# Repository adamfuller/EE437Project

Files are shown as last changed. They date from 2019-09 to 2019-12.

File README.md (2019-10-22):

# EE437Project
Autonomous robot car with a smartphone interface

# TODO
- [x] Code for servo
- [x] Add screw holes to board (Adam - 10/16)
- [x] Incorporate Arduino IC into board (Adam - 10/15)
- [x] Add signal lights (forward, backward, turn)
- [x] Design signal lights board
- [ ] Finalize Controller Board Design
- [ ] Submit board design and parts list
- [ ] Assemble board
- [ ] Test board

# Parts List
## Controller Board
- [ ] 1x ATMega328 IC
- [ ] 1x 16 MHz Crystal
- [ ] 1x 28pin socket
- [ ] 1x 4 pin header - male
- [ ] 1x 3 pin header - male
- [ ] 1x 6 pin header - female 90°
- [ ] 2x 2 slot terminal blocks
- [ ] 2x 2x6 header - male
- [ ] 1x power jack
- [ ] 8x 1n4004 diodes
- [ ] 2x 220uF capacitor
- [ ] 2x 20pF capacitor
- [ ] 2x 1k resistor
- [ ] 1x 2k resistor
- [ ] 1x 5mm LED
- [ ] Wire

## Signal Lights Board
- [ ] 12x 5mm LED
- [ ] 4x 300 resistor
- [ ] 4x 4 pin header - male

# Stand-alone Custom Board
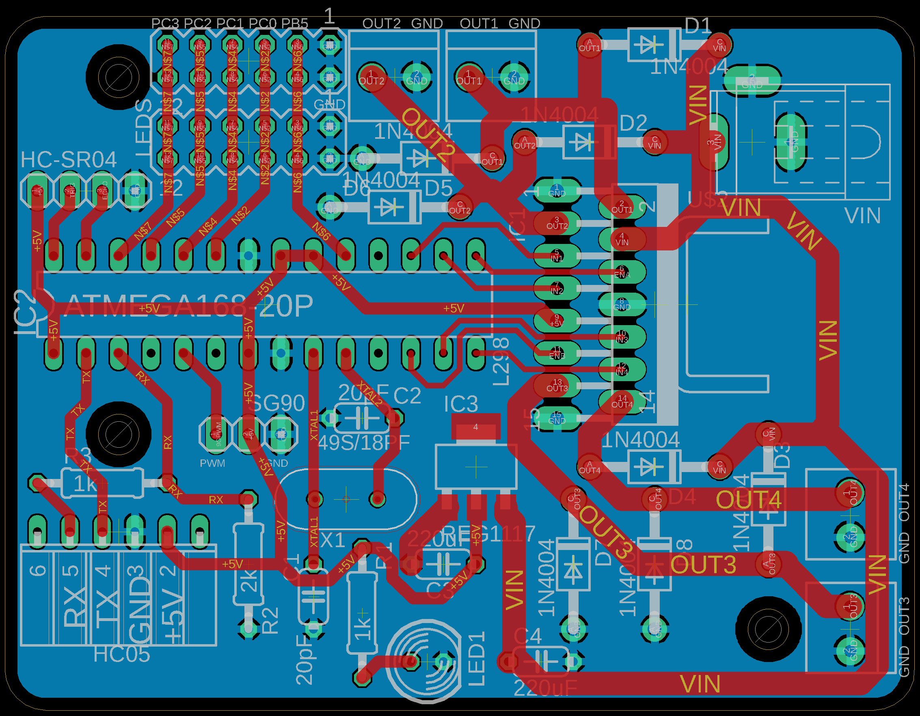
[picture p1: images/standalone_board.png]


# Stand-alone Custom Board Schematic
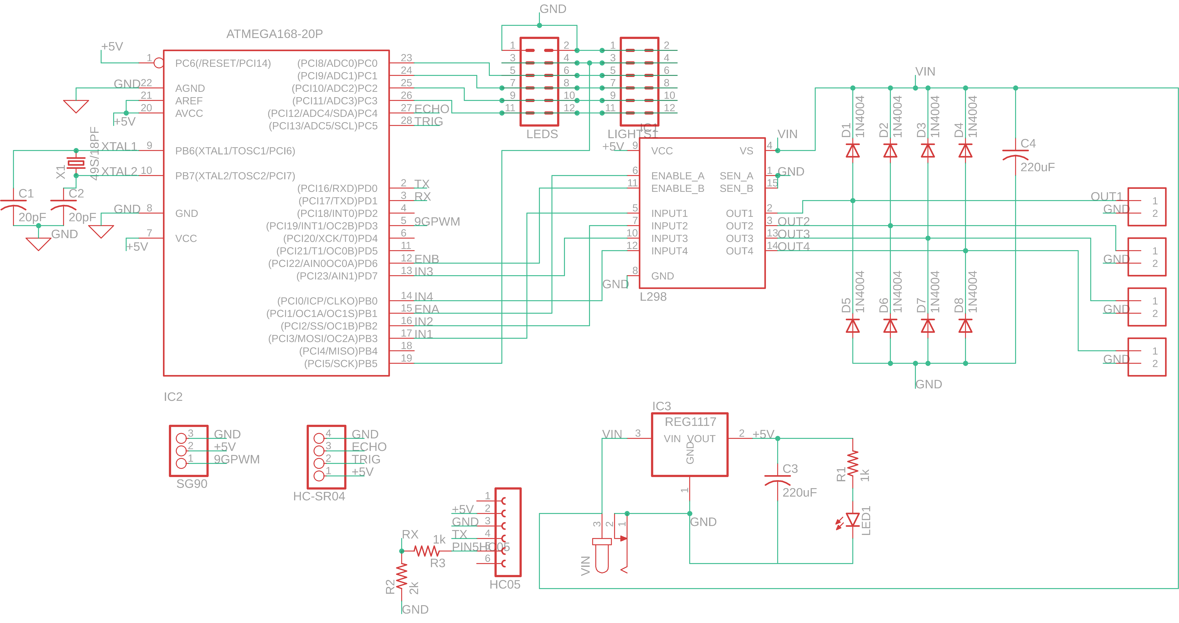
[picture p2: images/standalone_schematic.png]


# Stand-alone Custom Board Manufacturing Preview

## Top
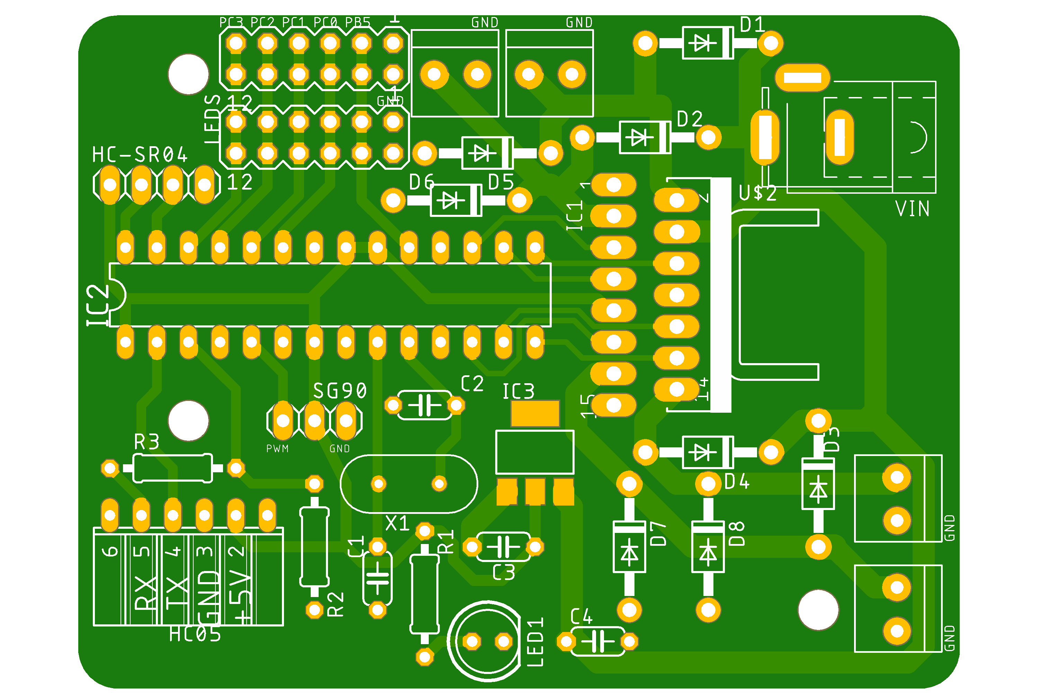
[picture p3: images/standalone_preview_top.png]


## Bottom
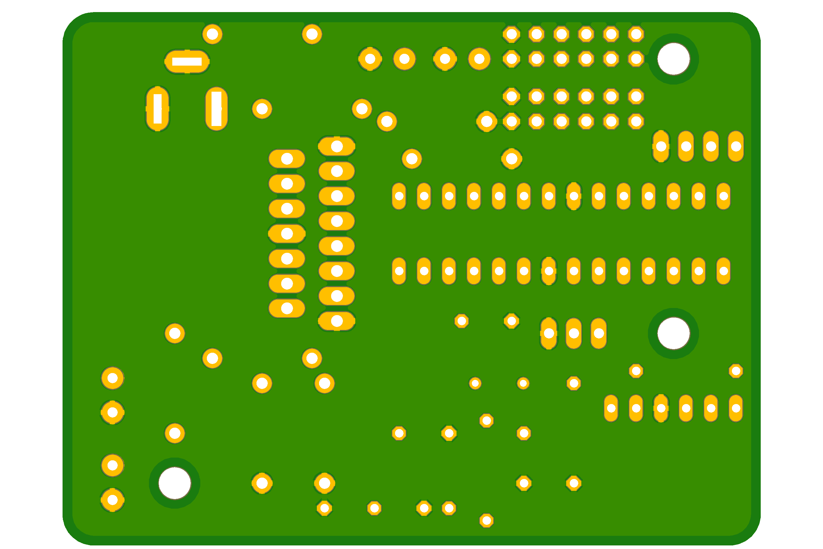
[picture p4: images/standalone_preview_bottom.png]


# Custom Shield Board
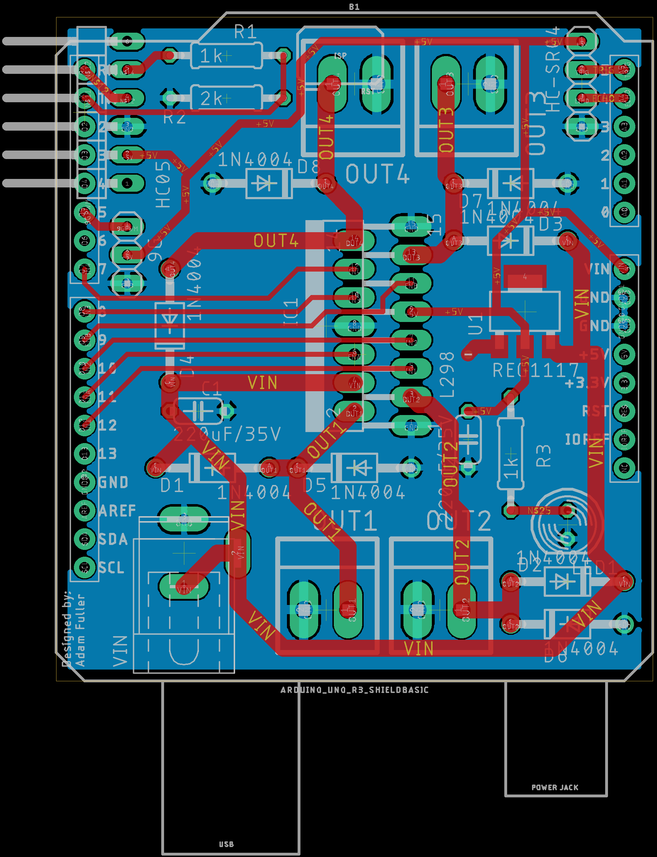
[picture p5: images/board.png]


# Custom Shield Schematic
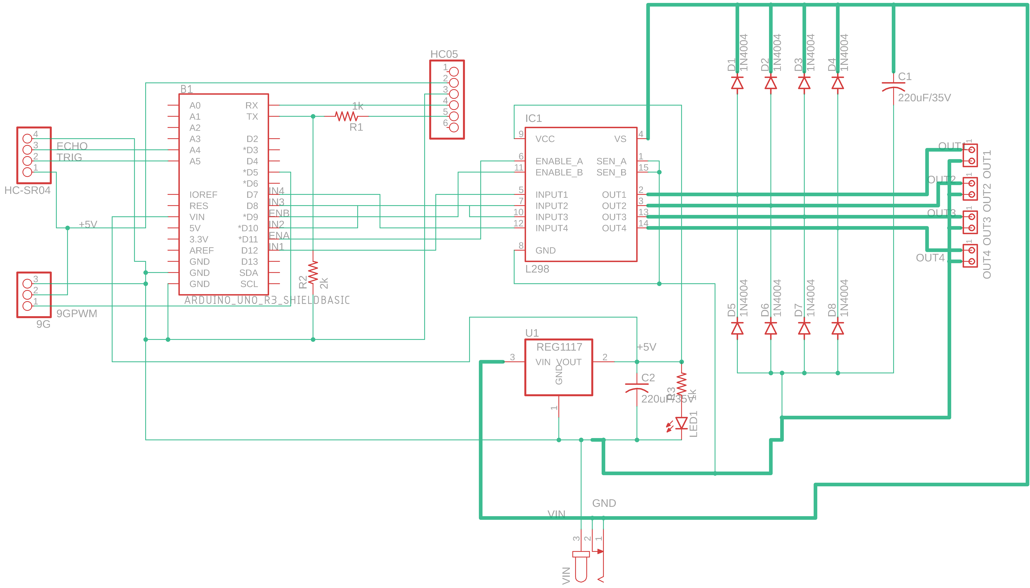
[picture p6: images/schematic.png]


# Custom Shield Manufacturing Preview

## Top
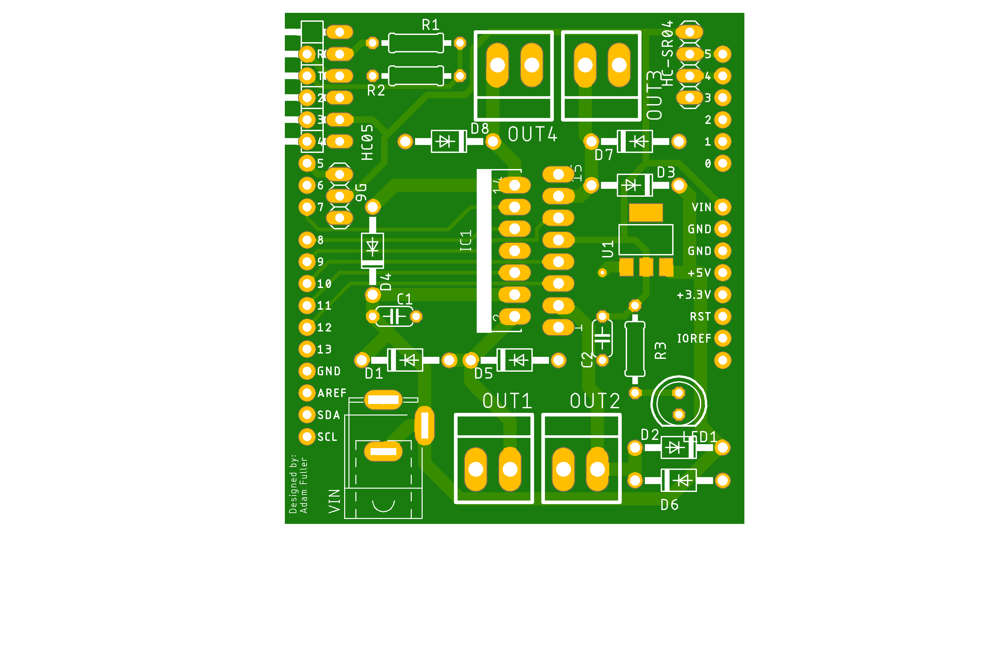
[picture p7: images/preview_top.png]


## Bottom
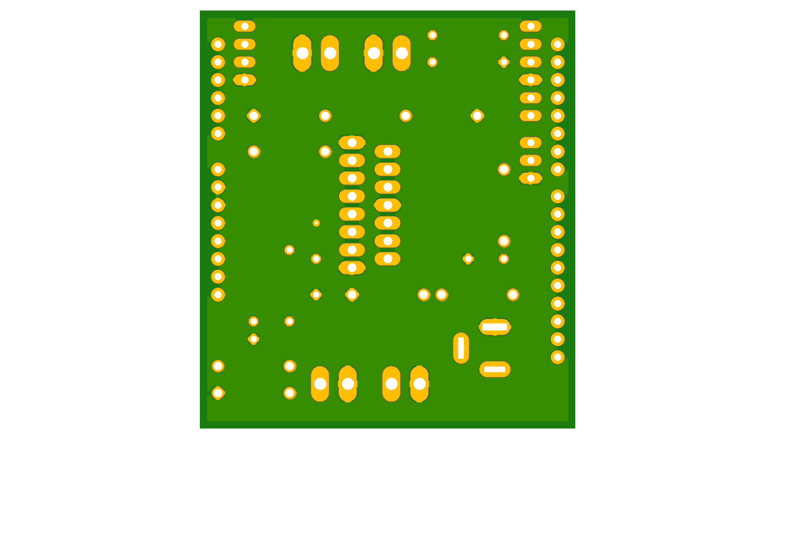
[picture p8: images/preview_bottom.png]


# Reduced Custom Board
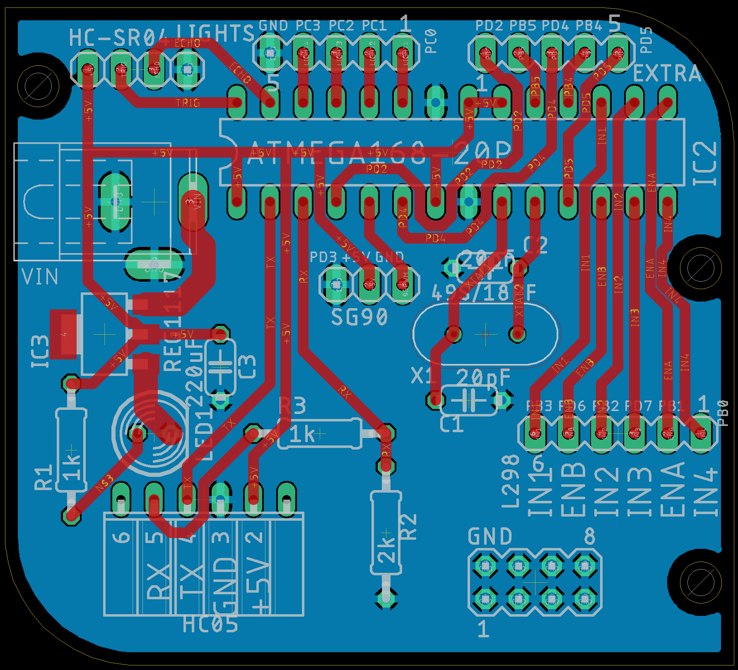
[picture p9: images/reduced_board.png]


# Reduced Custom Board Schematic
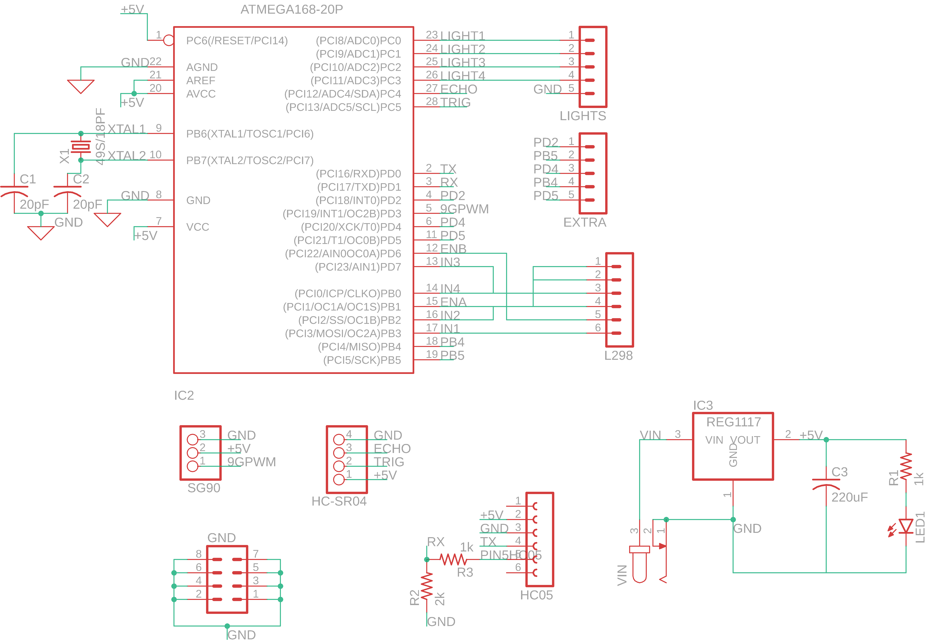
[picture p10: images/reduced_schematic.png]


# Reduced Custom Board Manufacturing Preview

## Top
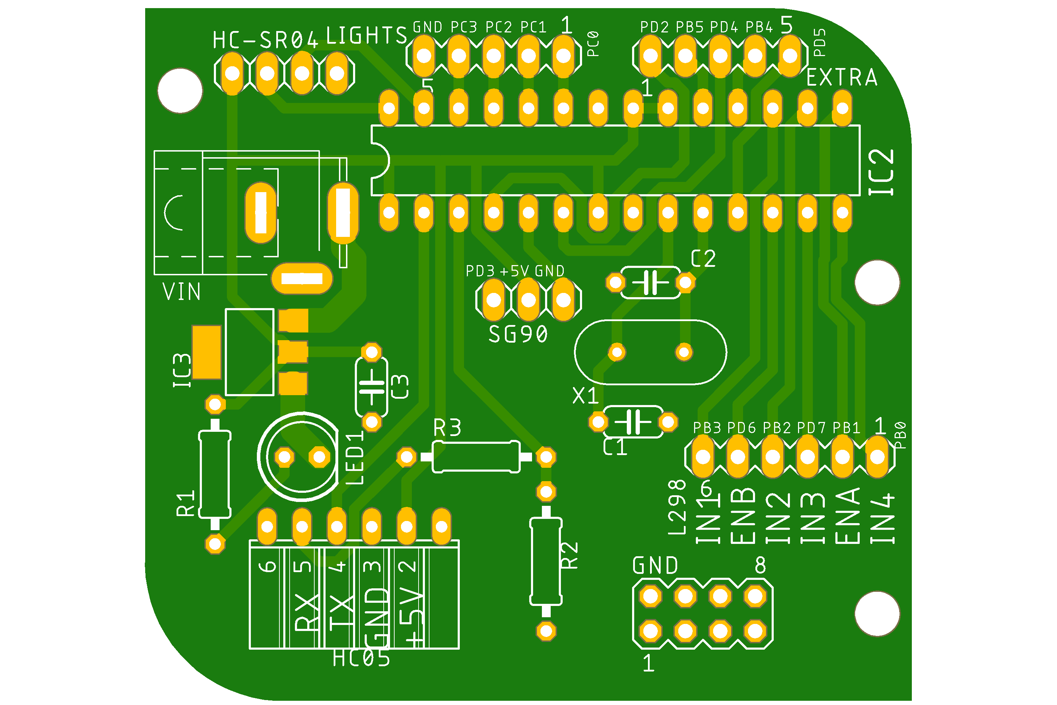
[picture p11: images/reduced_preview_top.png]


## Bottom
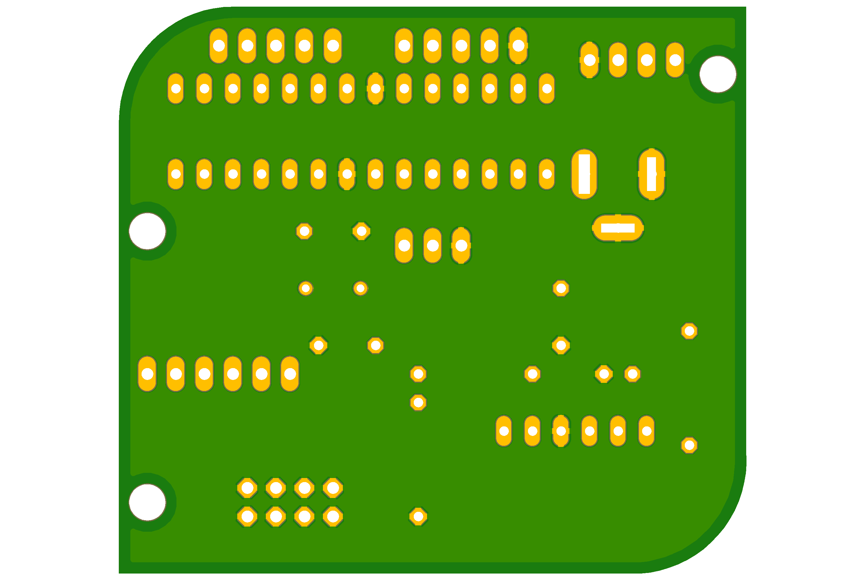
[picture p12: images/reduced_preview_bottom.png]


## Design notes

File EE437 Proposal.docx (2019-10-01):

EE437 Team 5

Adam Fuller

Isaiah Chamoun

Gavin Matthews

Description:

The project chosen by the members of Team 5 is titled “Autonomous robot car with a smartphone interface.” The goal of our project is to develop an application to control a 4-wheeled car as well as the Arduino code to interface with this. The phone and the car should communicate using Bluetooth. The minimum functionality of the car is to be capable of driving forward, backwards, turning right and left, as well as stopping. The car should communicate with an ultrasonic distance sensor to prevent itself from being driven into obstacles. A custom PCB will be designed to house the connections to the Bluetooth module, ultrasonic sensor, and the controls for the motor driver.

Parts List:

2x 8 Pin Header

1x 10 Pin Header

1x 6 Pin Header

2x 1 kΩ Resistor

1x 2 kΩ Resistor

8x 1N4004 Diodes

2x 2 Pin Terminal Block

1x 5mm Green LED

2x 220 µF 35V Capacitor

1x L298 IC

1x REG1117 Voltage Regulator

1x HC-SR04 Ultra sonic sensor

1x HC-05 Bluetooth module

4x DC Motors

1x SG90 Servo Motor

2x 18650 Batteries

1x Custom PCB

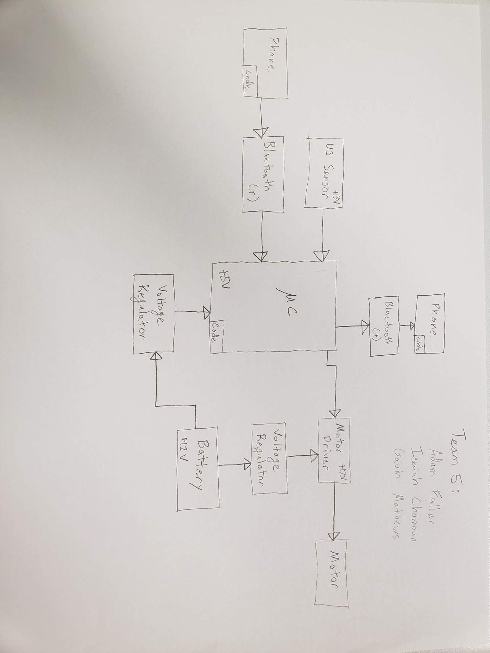
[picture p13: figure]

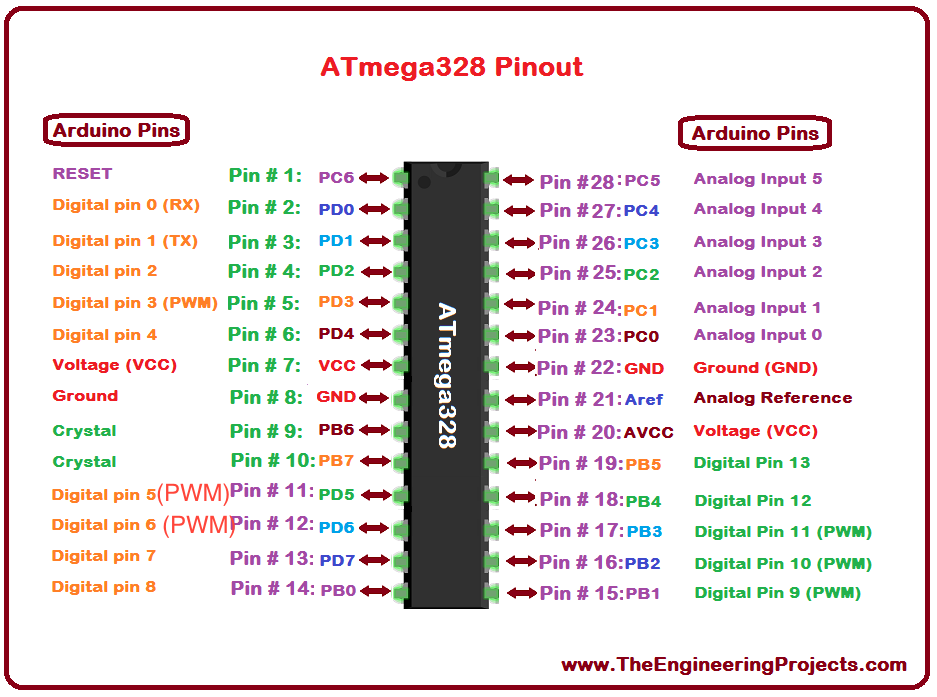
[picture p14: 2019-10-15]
images/ATmega328-Pinout.png

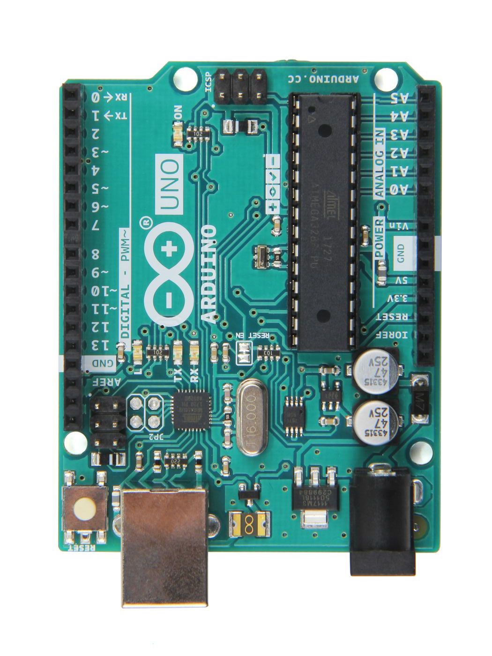
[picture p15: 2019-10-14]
images/arduinoUno.jpg

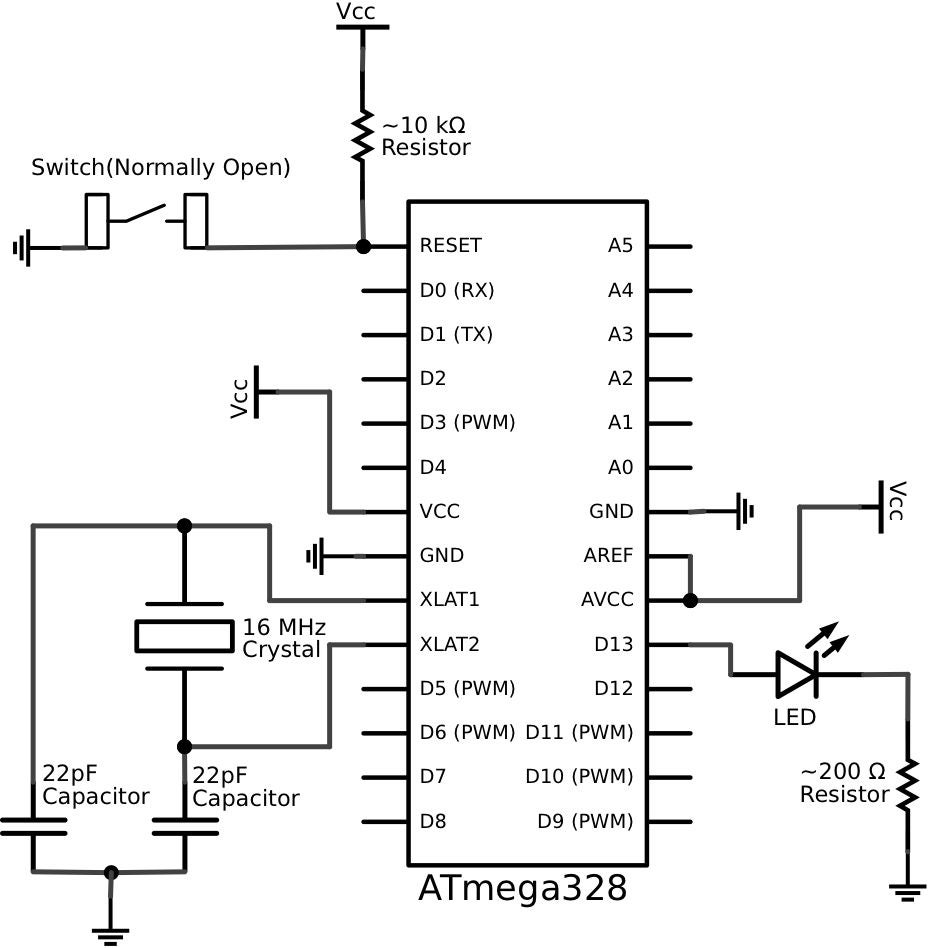
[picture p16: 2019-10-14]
images/atmega328Breadboard.jpg

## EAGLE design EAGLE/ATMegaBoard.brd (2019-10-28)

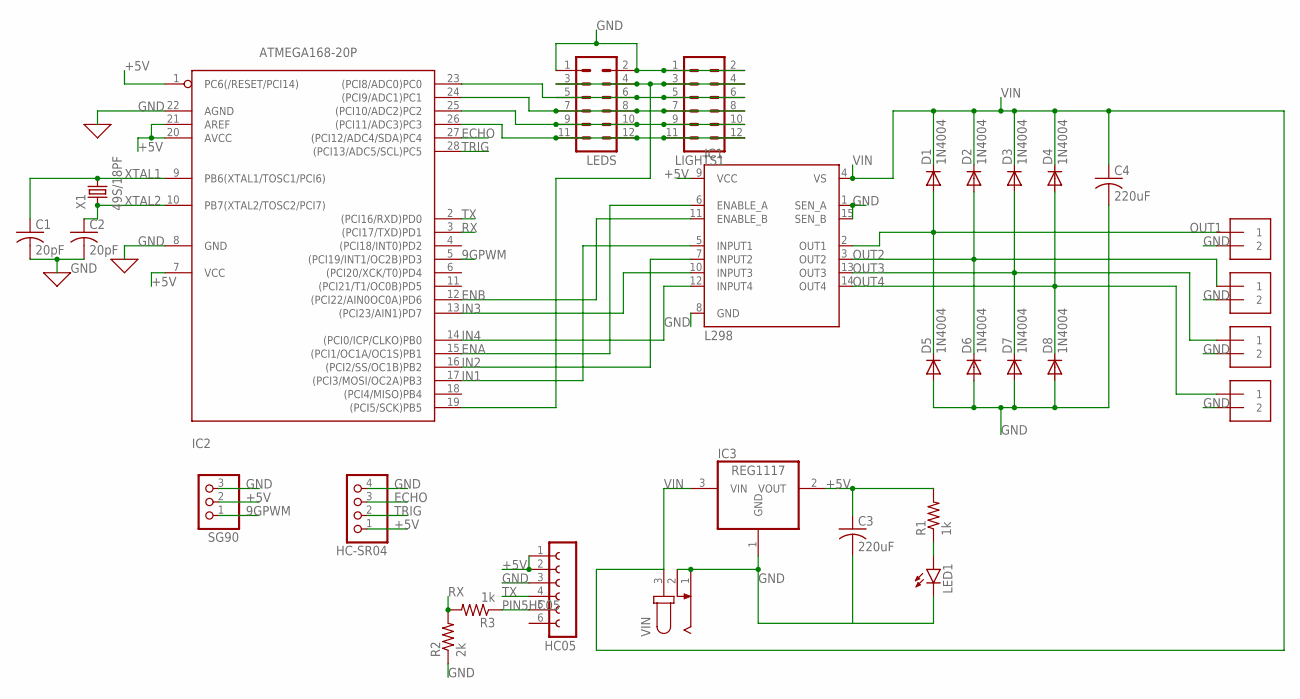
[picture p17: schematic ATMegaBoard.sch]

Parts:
C1, C2: 20pF; C050-024X044
C3, C4: 220uF; C050-024X044
D1, D2, D3, D4, D5, D6, D7, D8: 1N4004; DO41-10
HC05: FE06W
HC-SR04: PINHD-1X4; 1X04
IC1: L298; MULTIWATT-15
IC2: ATMEGA168-20P; DIL28-3
IC3: REG1117; SOT223
LED1: LED5MM
LEDS: MA06-2
LIGHTS1: MA06-2
OUT1, OUT2, OUT3, OUT4: 1X2-3.5MM
R1, R3: 1k; 0207/10
R2: 2k; 0207/10
SG90: PINHD-1X3; 1X03
VIN: JACK-PLUG1; SPC4078
X1: 49S/18PF; XTAL_HC49

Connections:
9GPWM: IC2.5 ((PCI19/INT1/OC2B)PD3), SG90.1
+5V: C3.1, HC05.1, HC05.2, HC-SR04.1, IC1.9 (VCC), IC2.1 (PC6(/RESET/PCI14)), IC2.7 (VCC), IC2.20 (AVCC), IC2.21 (AREF), IC3.2 (VOUT), R1.2, SG90.2
ECHO: HC-SR04.3, IC2.27 ((PCI12/ADC4/SDA)PC4)
ENA: IC1.6 (ENABLE_A), IC2.15 ((PCI1/OC1A/OC1S)PB1)
ENB: IC1.11 (ENABLE_B), IC2.12 ((PCI22/AIN0OC0A)PD6)
GND: C1.2, C2.2, C3.2, C4.2, D5.A, D6.A, D7.A, D8.A, HC05.3, HC-SR04.4, IC1.1 (SEN_A), IC1.8 (GND), IC1.15 (SEN_B), IC2.8 (GND), IC2.22 (AGND), IC3.1 (GND), LED1.K (C), LEDS.1, LEDS.2, LIGHTS1.1, LIGHTS1.2, OUT1.2, OUT2.2, OUT3.2, OUT4.2, R2.1, SG90.3, VIN.1, VIN.2
IN1: IC1.5 (INPUT1), IC2.17 ((PCI3/MOSI/OC2A)PB3)
IN2: IC1.7 (INPUT2), IC2.16 ((PCI2/SS/OC1B)PB2)
IN3: IC1.10 (INPUT3), IC2.13 ((PCI23/AIN1)PD7)
IN4: IC1.12 (INPUT4), IC2.14 ((PCI0/ICP/CLKO)PB0)
unnamed: IC2.23 ((PCI8/ADC0)PC0), LEDS.5, LEDS.6, LIGHTS1.5, LIGHTS1.6
unnamed: LED1.A, R1.1
unnamed: IC2.24 ((PCI9/ADC1)PC1), LEDS.7, LEDS.8, LIGHTS1.7, LIGHTS1.8
unnamed: IC2.25 ((PCI10/ADC2)PC2), LEDS.9, LEDS.10, LIGHTS1.9, LIGHTS1.10
unnamed: IC2.19 ((PCI5/SCK)PB5), LEDS.3, LEDS.4, LIGHTS1.3, LIGHTS1.4
unnamed: IC2.26 ((PCI11/ADC3)PC3), LEDS.11, LEDS.12, LIGHTS1.11, LIGHTS1.12
OUT1: D1.A, D5.C, IC1.2 (OUT1), OUT1.1
OUT2: D2.A, D6.C, IC1.3 (OUT2), OUT2.1
OUT3: D3.A, D7.C, IC1.13 (OUT3), OUT3.1
OUT4: D4.A, D8.C, IC1.14 (OUT4), OUT4.1
PIN5HC05: HC05.5, R3.1
RX: IC2.3 ((PCI17/TXD)PD1), R2.2, R3.2
TRIG: HC-SR04.2, IC2.28 ((PCI13/ADC5/SCL)PC5)
TX: HC05.4, IC2.2 ((PCI16/RXD)PD0)
VIN: C4.1, D1.C, D2.C, D3.C, D4.C, IC1.4 (VS), IC3.3 (VIN), VIN.3
XTAL1: C1.1, IC2.9 (PB6(XTAL1/TOSC1/PCI6)), X1.2
XTAL2: C2.1, IC2.10 (PB7(XTAL2/TOSC2/PCI7)), X1.1

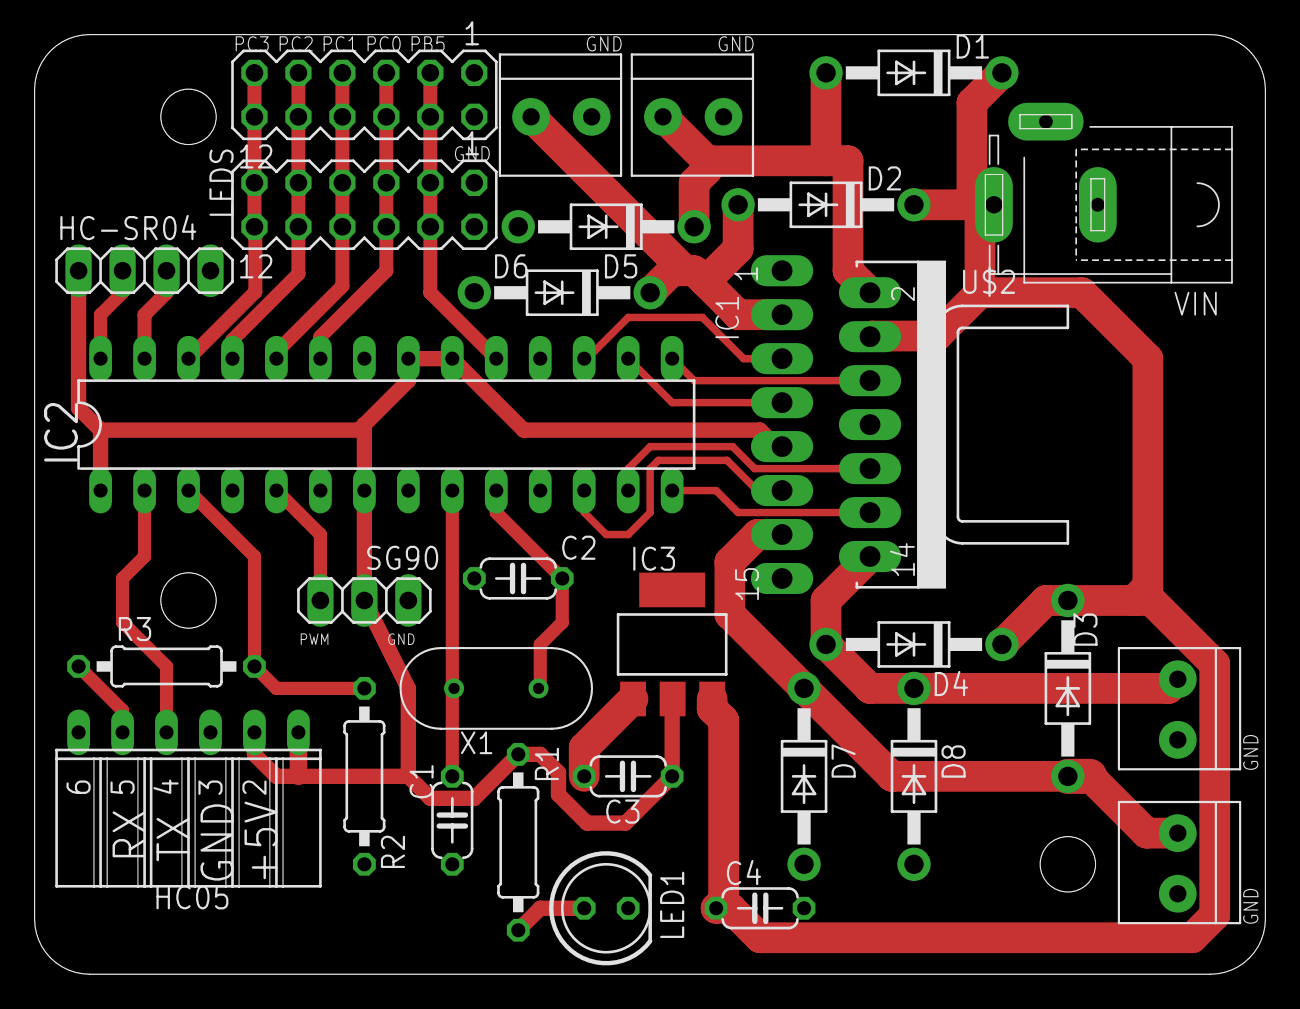
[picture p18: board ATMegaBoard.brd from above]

Board: 2 copper layers, 71.1 x 54.3 mm, 31 parts (0 on the bottom side), 27 nets.

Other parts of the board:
U$2: D03S

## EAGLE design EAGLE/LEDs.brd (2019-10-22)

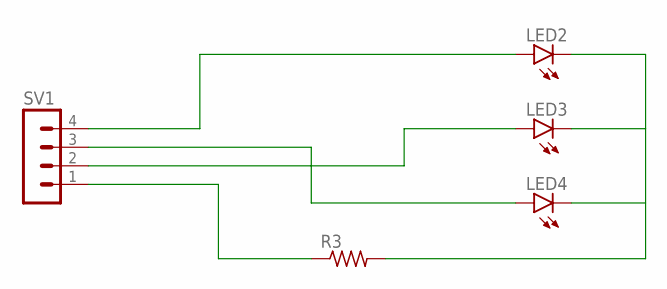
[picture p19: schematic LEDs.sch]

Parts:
LED2, LED3, LED4: LED5MM
R3: R-US_0204/7; 0204/7
SV1: MA04-1

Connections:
unnamed: LED2.A, SV1.4
unnamed: LED4.A, SV1.3
unnamed: LED3.A, SV1.2
unnamed: LED2.K (C), LED3.K (C), LED4.K (C), R3.2
unnamed: R3.1, SV1.1

Board: 2 copper layers, 5 parts (0 on the bottom side), 5 nets, no tracks yet.

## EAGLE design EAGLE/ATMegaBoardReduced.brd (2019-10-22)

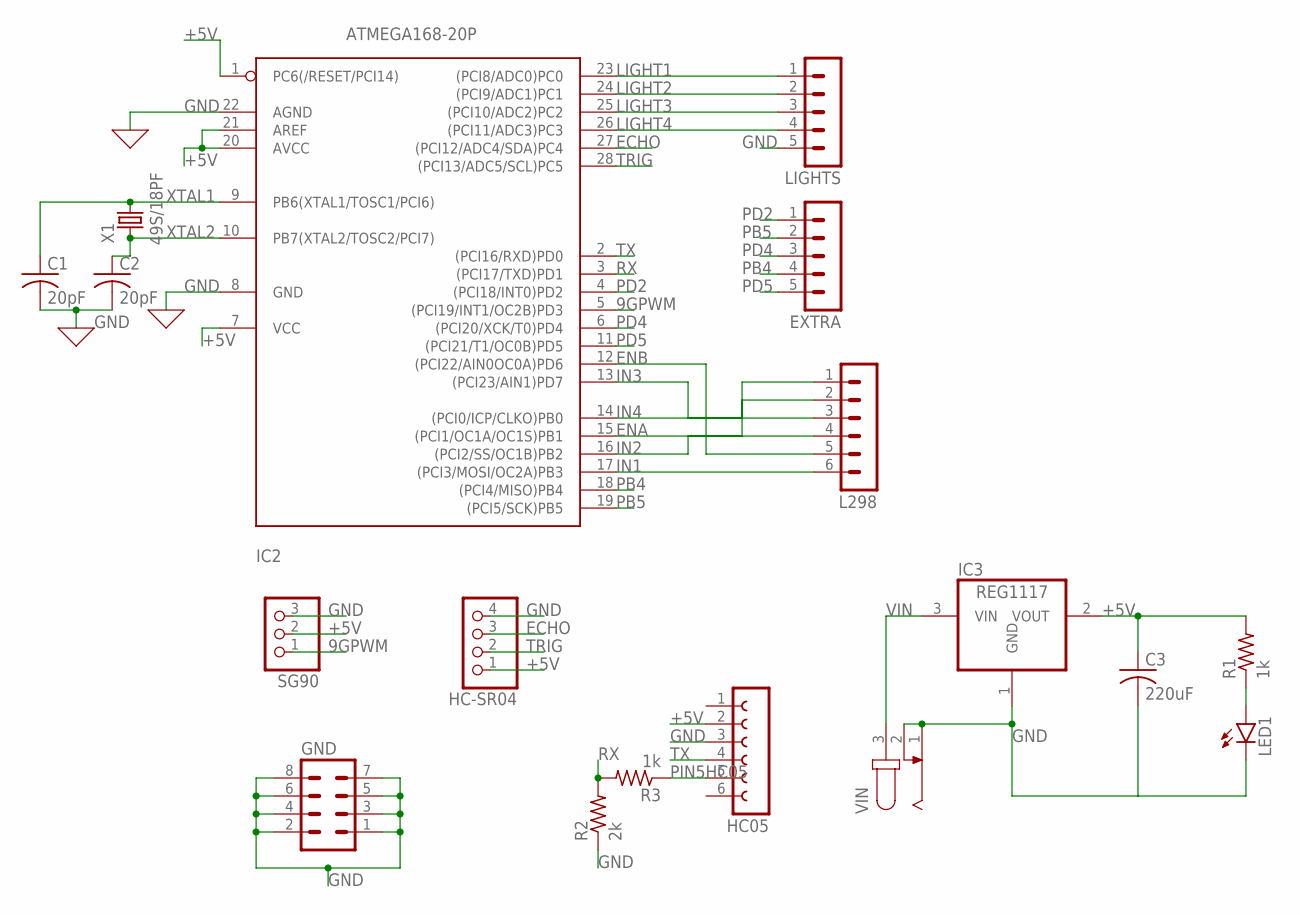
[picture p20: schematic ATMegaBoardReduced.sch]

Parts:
C1, C2: 20pF; C050-024X044
C3: 220uF; C050-024X044
EXTRA: MA05-1
GND: MA04-2
HC05: FE06W
HC-SR04: PINHD-1X4; 1X04
IC2: ATMEGA168-20P; DIL28-3
IC3: REG1117; SOT223
L298: MA06-1
LED1: LED5MM
LIGHTS: MA05-1
R1, R3: 1k; 0207/10
R2: 2k; 0207/10
SG90: PINHD-1X3; 1X03
VIN: JACK-PLUG1; SPC4078
X1: 49S/18PF; XTAL_HC49

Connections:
9GPWM: IC2.5 ((PCI19/INT1/OC2B)PD3), SG90.1
+5V: C3.1, HC05.2, HC-SR04.1, IC2.1 (PC6(/RESET/PCI14)), IC2.7 (VCC), IC2.20 (AVCC), IC2.21 (AREF), IC3.2 (VOUT), R1.2, SG90.2
ECHO: HC-SR04.3, IC2.27 ((PCI12/ADC4/SDA)PC4)
ENA: IC2.15 ((PCI1/OC1A/OC1S)PB1), L298.2
ENB: IC2.12 ((PCI22/AIN0OC0A)PD6), L298.5
GND: C1.2, C2.2, C3.2, GND.1, GND.2, GND.3, GND.4, GND.5, GND.6, GND.7, GND.8, HC05.3, HC-SR04.4, IC2.8 (GND), IC2.22 (AGND), IC3.1 (GND), LED1.K (C), LIGHTS.5, R2.1, SG90.3, VIN.1, VIN.2
IN1: IC2.17 ((PCI3/MOSI/OC2A)PB3), L298.6
IN2: IC2.16 ((PCI2/SS/OC1B)PB2), L298.4
IN3: IC2.13 ((PCI23/AIN1)PD7), L298.3
IN4: IC2.14 ((PCI0/ICP/CLKO)PB0), L298.1
LIGHT1: IC2.23 ((PCI8/ADC0)PC0), LIGHTS.1
LIGHT2: IC2.24 ((PCI9/ADC1)PC1), LIGHTS.2
LIGHT3: IC2.25 ((PCI10/ADC2)PC2), LIGHTS.3
LIGHT4: IC2.26 ((PCI11/ADC3)PC3), LIGHTS.4
unnamed: LED1.A, R1.1
PB4: EXTRA.4, IC2.18 ((PCI4/MISO)PB4)
PB5: EXTRA.2, IC2.19 ((PCI5/SCK)PB5)
PD2: EXTRA.1, IC2.4 ((PCI18/INT0)PD2)
PD4: EXTRA.3, IC2.6 ((PCI20/XCK/T0)PD4)
PD5: EXTRA.5, IC2.11 ((PCI21/T1/OC0B)PD5)
PIN5HC05: HC05.5, R3.1
RX: IC2.3 ((PCI17/TXD)PD1), R2.2, R3.2
TRIG: HC-SR04.2, IC2.28 ((PCI13/ADC5/SCL)PC5)
TX: HC05.4, IC2.2 ((PCI16/RXD)PD0)
VIN: IC3.3 (VIN), VIN.3
XTAL1: C1.1, IC2.9 (PB6(XTAL1/TOSC1/PCI6)), X1.2
XTAL2: C2.1, IC2.10 (PB7(XTAL2/TOSC2/PCI7)), X1.1

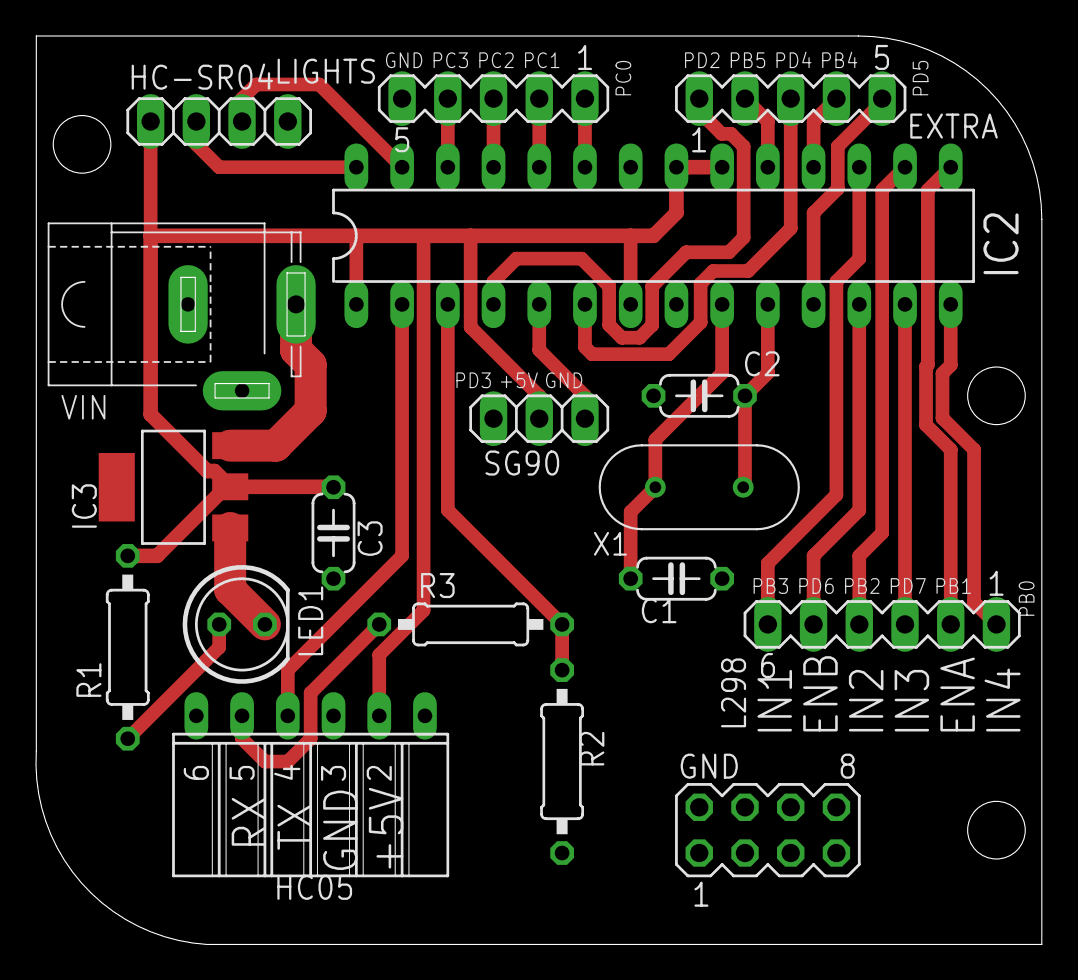
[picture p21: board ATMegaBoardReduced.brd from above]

Board: 2 copper layers, 55.9 x 50.5 mm, 18 parts (0 on the bottom side), 27 nets.

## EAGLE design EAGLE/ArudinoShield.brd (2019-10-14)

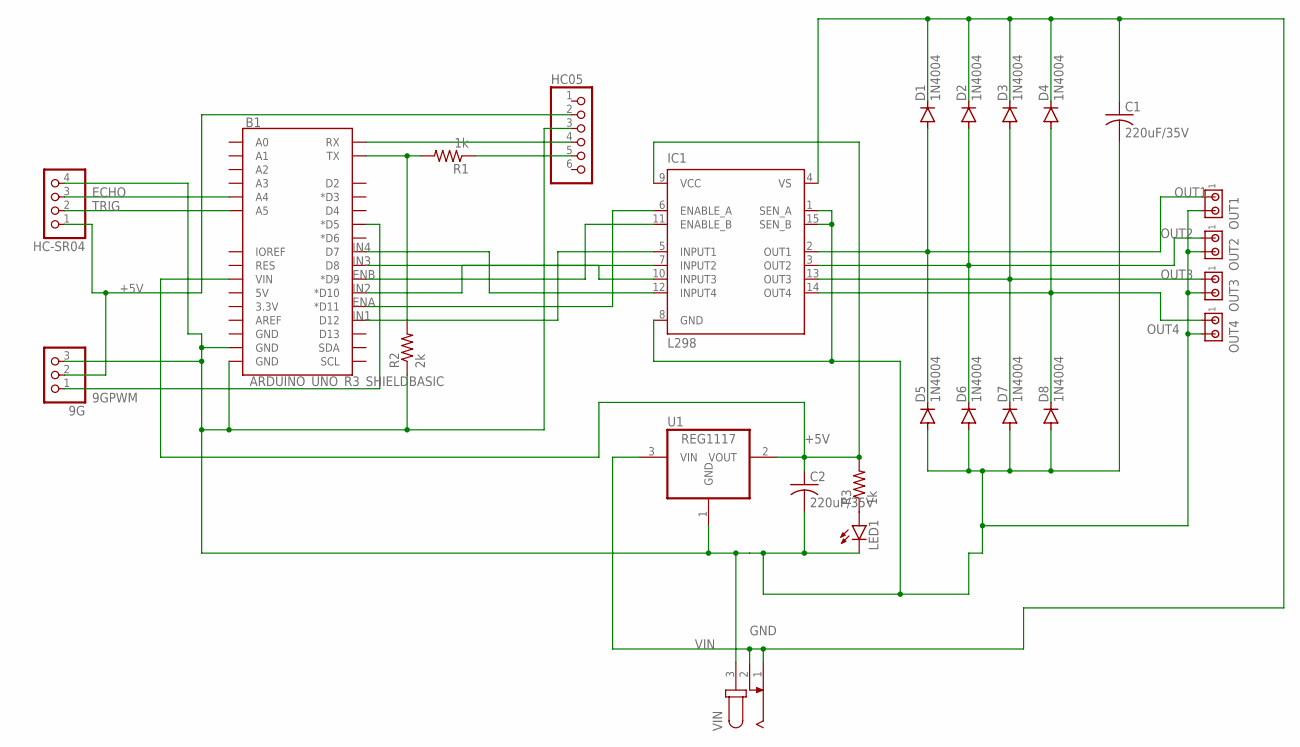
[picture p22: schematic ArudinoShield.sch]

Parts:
9G: PINHD-1X3; 1X03
B1: ARDUINO_UNO_R3_SHIELDBASIC; UNO_R3_SHIELD
C1, C2: 220uF/35V; C050-024X044
D1, D2, D3, D4, D5, D6, D7, D8: 1N4004; DO41-10
HC05: PINHD-1X6/90; 1X06/90
HC-SR04: PINHD-1X4; 1X04
IC1: L298; MULTIWATT-15
LED1: LED5MM
OUT1, OUT2, OUT3, OUT4: MTA02-156; 1X2MTA
R1, R3: 1k; 0207/10
R2: 2k; 0207/10
U1: REG1117; SOT223
VIN: JACK-PLUG1; SPC4078

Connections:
9GPWM: 9G.1, B1.D5 (*D5)
+5V: 9G.2, B1.VIN, C2.1, HC05.2, HC-SR04.1, IC1.9 (VCC), R3.2, U1.2 (VOUT)
ECHO: B1.A4, HC-SR04.3
ENA: B1.D11 (*D11), IC1.6 (ENABLE_A)
ENB: B1.D9 (*D9), IC1.11 (ENABLE_B)
GND: 9G.3, B1.GND@0 (GND), B1.GND@1 (GND), C1.2, C2.2, D5.A, D6.A, D7.A, D8.A, HC05.3, HC-SR04.4, IC1.1 (SEN_A), IC1.8 (GND), IC1.15 (SEN_B), LED1.K (C), OUT1.2, OUT2.2, OUT3.2, OUT4.2, R2.1, U1.1 (GND), VIN.3
IN1: B1.D12, IC1.5 (INPUT1)
IN2: B1.D10 (*D10), IC1.7 (INPUT2)
IN3: B1.D8, IC1.10 (INPUT3)
IN4: B1.D7, IC1.12 (INPUT4)
unnamed: B1.TX, R1.2, R2.2
unnamed: B1.RX, HC05.4
unnamed: HC05.5, R1.1
unnamed: LED1.A, R3.1
OUT1: D1.A, D5.C, IC1.2 (OUT1), OUT1.1
OUT2: D2.A, D6.C, IC1.3 (OUT2), OUT2.1
OUT3: D3.A, D7.C, IC1.13 (OUT3), OUT3.1
OUT4: D4.A, D8.C, IC1.14 (OUT4), OUT4.1
TRIG: B1.A5, HC-SR04.2
VIN: C1.1, D1.C, D2.C, D3.C, D4.C, IC1.4 (VS), U1.3 (VIN), VIN.1, VIN.2

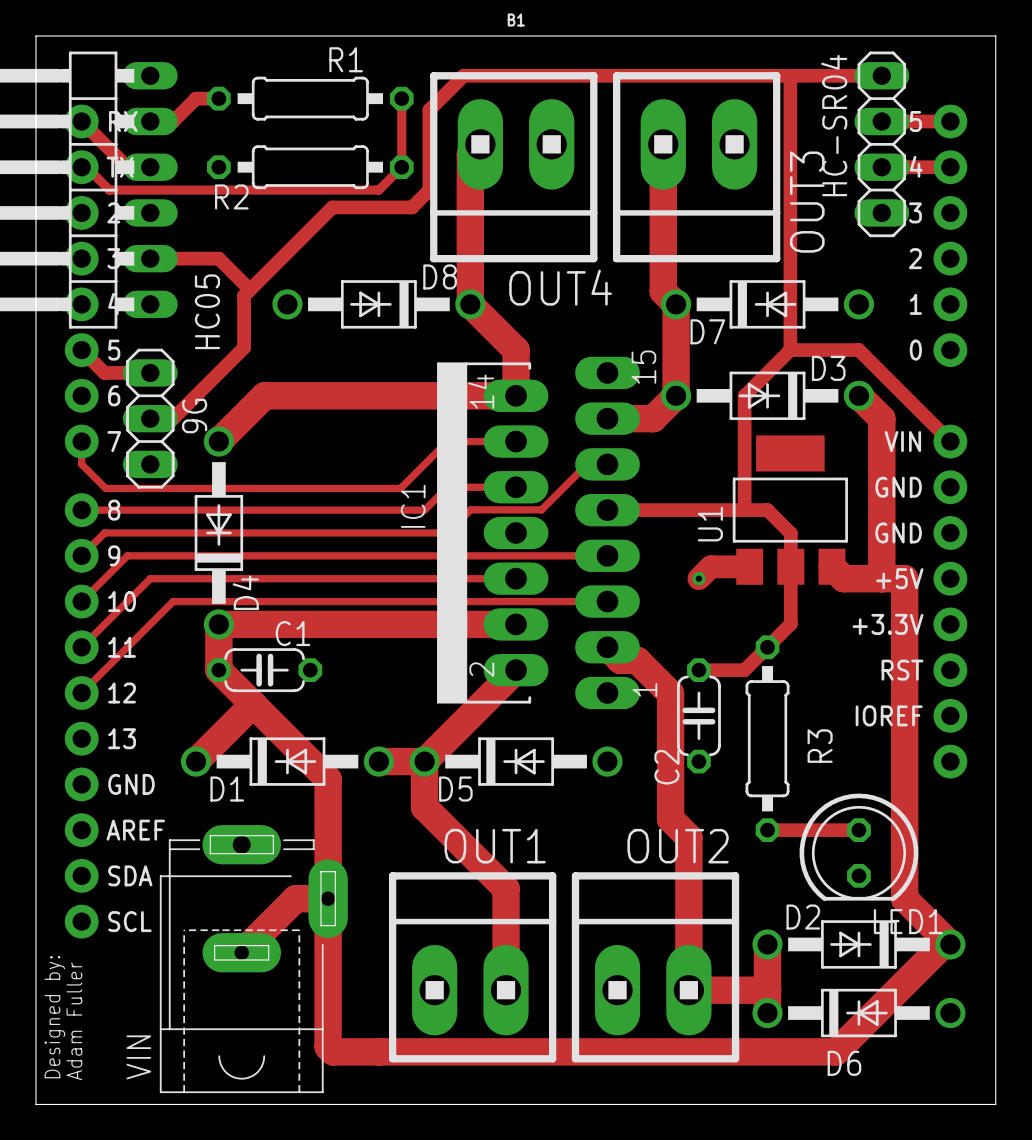
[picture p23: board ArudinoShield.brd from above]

Board: 2 copper layers, 53.3 x 59.4 mm, 25 parts (0 on the bottom side), 20 nets.

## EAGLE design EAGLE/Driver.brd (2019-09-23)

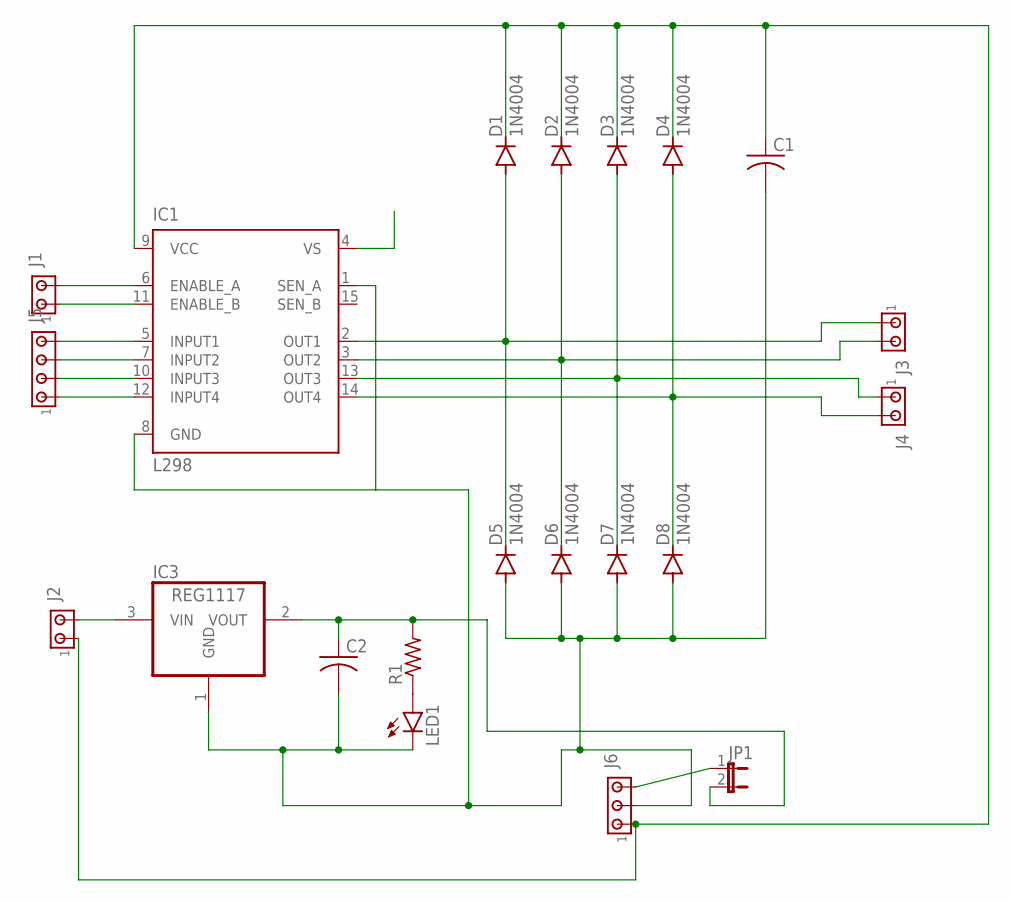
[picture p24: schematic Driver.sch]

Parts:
C1, C2: C-US050-024X044; C050-024X044
D1, D2, D3, D4, D5, D6, D7, D8: 1N4004; DO41-10
IC1: L298; MULTIWATT-15
IC3: REG1117; SOT223
J1, J2, J3, J4: MTA02-156; 1X2MTA
J5: MTA04-156; 1X4MTA
J6: MTA03-100; 10X03MTA
JP1: JP1E; JP1
LED1: LED5MM
R1: R-US_0207/10; 0207/10

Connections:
unnamed: D1.A, D5.C, IC1.2 (OUT1), J3.1
unnamed: D2.A, D6.C, IC1.3 (OUT2), J3.2
unnamed: D3.A, D7.C, IC1.13 (OUT3), J4.1
unnamed: D4.A, D8.C, IC1.14 (OUT4), J4.2
unnamed: IC1.6 (ENABLE_A), J1.2
unnamed: IC1.11 (ENABLE_B), J1.1
unnamed: IC1.5 (INPUT1), J5.4
unnamed: IC1.7 (INPUT2), J5.3
unnamed: IC1.10 (INPUT3), J5.2
unnamed: IC1.12 (INPUT4), J5.1
unnamed: C1.2, C2.2, D5.A, D6.A, D7.A, D8.A, IC1.1 (SEN_A), IC1.8 (GND), IC3.1 (GND), J6.2, LED1.K (C)
unnamed: J6.3, JP1.1
unnamed: LED1.A, R1.1
unnamed: C2.1, IC3.2 (VOUT), JP1.2, R1.2
unnamed: IC3.3 (VIN), J2.2
unnamed: C1.1, D1.C, D2.C, D3.C, D4.C, IC1.9 (VCC), J2.1, J6.1

Board: 2 copper layers, 21 parts (0 on the bottom side), 16 nets, no tracks yet.

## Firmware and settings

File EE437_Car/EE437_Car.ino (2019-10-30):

#include <Servo.h>


#define ECHO_PIN  A4 // PC4
#define TRIG_PIN  A5 // PC5
#define ENA_PIN   5
#define ENB_PIN   11
#define IN1_PIN   6 // Right forward
#define IN2_PIN   7 // Right backward
#define IN3_PIN   8 // Left backward
#define IN4_PIN   9 // Left forward
#define SERVO_PIN     3 

uint8_t btOutput;
int intent, extent;
uint8_t cache[8] = {0x00, 0x00, 0x00, 0x00, 0x00, 0x00, 0x00, 0x00};
bool checkedLastTime = false;
bool shouldBrake;
Servo servo;

int getDistance() {
  digitalWrite(TRIG_PIN, LOW);
  delayMicroseconds(2);
  digitalWrite(TRIG_PIN, HIGH);
  delayMicroseconds(10);
  digitalWrite(TRIG_PIN, LOW);
  return (int)pulseIn(ECHO_PIN, HIGH, 1583) / 58;
}

void brake(){
  analogWrite(ENA_PIN, 0);
  analogWrite(ENB_PIN, 0);
  analogWrite(IN1_PIN, 0);
//  PORTD&=0x3F; // Set IN2 and IN3 low
  analogWrite(IN2_PIN, 0);
  analogWrite(IN3_PIN, 0);
  analogWrite(IN4_PIN, 0);
}

void spinRight(){
  analogWrite(ENA_PIN, 255);
  analogWrite(ENB_PIN, 255);
  analogWrite(IN1_PIN, 0);
  analogWrite(IN2_PIN, 255);
  analogWrite(IN3_PIN, 0);
  analogWrite(IN4_PIN, 255);
}

void spinLeft(){
  analogWrite(ENA_PIN, 255);
  analogWrite(ENB_PIN, 255);
  analogWrite(IN1_PIN, 255);
  analogWrite(IN2_PIN, 0);
  analogWrite(IN3_PIN, 255);
  analogWrite(IN4_PIN, 0);
}

int steeringAngle(){
  int leftPower = (int)((((cache[0x06]) & 0x1F) / 31.0) * 255 );
  int rightPower = (int)((((cache[0x05]) & 0x1F) / 31.0) * 255 );
  if (leftPower == rightPower) return 90;
  return (int)((rightPower * 1.0 / (rightPower + leftPower) * 1.0) * 178) + 1;
}

void performTask(int task){
  switch (task){
    case 0x00:
      brake();
      break;
    case 0x01:
      spinRight();
      break;
    case 0x02:
      spinLeft();
      break;
    default:
      break;
  }
}

void setup() {
  Serial.begin(9600);
  pinMode(ECHO_PIN, INPUT);
  pinMode(TRIG_PIN, OUTPUT);
  pinMode(IN1_PIN, OUTPUT);
  pinMode(IN2_PIN, OUTPUT);
  pinMode(IN3_PIN, OUTPUT);
  pinMode(IN4_PIN, OUTPUT);
  pinMode(ENA_PIN, OUTPUT);
  pinMode(ENB_PIN, OUTPUT);
  servo.attach(SERVO_PIN);

  pinMode(LED_BUILTIN, OUTPUT);
}

void loop() {
  // Only check to brake every other time
  if (!checkedLastTime){
    int dist = getDistance();  
    // Check if we should brake.
    shouldBrake = abs(dist) <= 20 && abs(dist) != 0;
  }
  
  checkedLastTime = !checkedLastTime;

  // Check for next command(s)
  for (int i = 0; i< 10; i++){
    if (Serial.available()){
      btOutput = Serial.read();
      cache[(btOutput & 0xE0) >> 5] = btOutput;
    } else {
      break;
    }
  }

  if (shouldBrake){

    // Ensure we shouldn't be braking or going in reverse
    if ( cache[0x07] != 0xE0 && (cache[0x02]&0x1F != 0x00 || cache[0x03]&0x1F != 0x00) ){
      analogWrite(IN2_PIN, (int)((((cache[0x02]) & 0x1F) / 31.0) * 255 ));
      analogWrite(IN3_PIN, (int)((((cache[0x03]) & 0x1F) / 31.0) * 255 ));
      analogWrite(ENA_PIN, (int)((((cache[0x05]) & 0x1F) / 31.0) * 255 ));
      analogWrite(ENB_PIN, (int)((((cache[0x06]) & 0x1F) / 31.0) * 255 ));
    } else {
      brake();
    }
    return;
  }

  servo.write(steeringAngle());

  for (intent = 0x01; intent < 0x08; intent++){
    extent = (int)((((cache[intent]) & 0x1F) / 31.0) * 255 );

    // Continue if this command is used (bits 5-7 cleared)
    if ((cache[intent] & 0xE0) == 0x00) continue;
    
    // return the command to the controller ( this is used to reduce sending repeat commands )
    Serial.print(cache[intent]);
    
    switch (intent){
      case 0x01:
        // IN1
        analogWrite(IN1_PIN, extent);
        break;
      case 0x02:
        // IN2
        analogWrite(IN2_PIN, extent);
        break;
      case 0x03:
        // IN3
        analogWrite(IN3_PIN, extent);
        break;
      case 0x04:
        // IN4
        analogWrite(IN4_PIN, extent);
        break;
      case 0x05:
        // ENA
        analogWrite(ENA_PIN, extent);
        break;
      case 0x06:
        // ENB
        analogWrite(ENB_PIN, extent);
        break;
       case 0x07:
        // Multi-command tasks
        performTask(cache[intent] & 0x1F);
        break;
      default:
        break;
    }
    // Set the command as used (clear bits 5-7)
    cache[intent] = cache[intent] & 0x1F;
  }
}

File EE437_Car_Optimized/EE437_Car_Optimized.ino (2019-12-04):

#include <Servo.h>


#define ECHO_PIN  A4 // PC4
#define TRIG_PIN  A5 // PC5
#define ENA_PIN   5
#define ENB_PIN   11
#define IN1_PIN   6 // Right forward
#define IN2_PIN   7 // Right backward
#define IN3_PIN   8 // Left backward
#define IN4_PIN   9 // Left forward
#define SERVO_PIN     3 


#define IN1_HIGH asm(" sbi 11, 6") //PORTD|=0x40 // 0b0100 0000
#define IN1_LOW asm(" cbi 11, 6") //PORTD&=0xBF  // 0b1011 1111
#define IN1_ENABLE asm(" sbi 10, 6") //DDRD&=0x40  // 0b0100 0000

#define IN2_HIGH asm(" sbi 11, 7") //PORTD|=0x80 // 0b1000 0000
#define IN2_LOW asm(" cbi 11, 7") //PORTD&=0x7F  // 0b0111 1111
#define IN2_ENABLE asm(" sbi 10, 7") //DDRD&=0x40  // 0b1000 0000

#define IN3_HIGH asm(" sbi 5, 0")//PORTB|=0x01 // 0b0000 0001
#define IN3_LOW asm(" cbi 5, 0")//PORTB&=0xFE  // 0b1111 1110
#define IN3_ENABLE asm(" sbi 4, 0") //DDRB&=0x01  // 0b0000 0001

#define IN4_HIGH asm(" sbi 5, 1")//PORTB|=0x02 // 0b0000 0010
#define IN4_LOW asm(" cbi 5, 1")//PORTB&=0xFD  // 0b1111 1101
#define IN4_ENABLE asm(" sbi 4, 1") //DDRB&=0x02  // 0b1000 0000

#define ENA_HIGH asm(" sbi 11, 5")//PORTD|=0x08 // 0b0000 1000
#define ENA_LOW asm(" cbi 11, 5")//PORTD&=0xF7  // 0b1111 0111
#define ENA_ENABLE asm(" sbi 10, 5") //DDRD&=0x08  // 0b1000 0000

#define ENB_HIGH asm(" sbi 5, 3")//PORTB|=0x08 // 0b0000 1000
#define ENB_LOW asm(" cbi 5, 3")//PORTB&=0xF7  // 0b1111 0111
#define ENB_ENABLE asm(" sbi 4, 3") //DDRB&=0x08  // 0b1000 0000

#define LED_HIGH asm(" sbi 5, 5")//PORTB|=0x20 // 0b0010 0000
#define LED_LOW asm(" cbi 5, 5")//PORTB&=0xF7  // 0b1111 0111
#define LED_ENABLE asm(" sbi 4, 5") //DDRB&=0x20  // 0b0010 0000

#define TRIG_HIGH asm(" sbi 8, 5")//PORTC|=0x20 // 0b0010 0000
#define TRIG_LOW asm(" cbi 8, 5")//PORTC&=0xDF  // 0b1101 1111
#define TRIG_ENABLE asm(" sbi 7, 5") //DDRC&=0x20  // 0b1000 0000

//#define SERVO_HIGH asm(" sbi 11, 3")//PORTD &= 0b0000 1000
//#define SERVO_LOW asm(" cbi 11, 3")//PORTD &= 0b1111 0111
//#define SERVO_ENABLE asm(" sbi 10, 3") //DDRD &= 0b0000 1000

#define ECHO_ENABLE asm(" cbi 7, 4") //DDRC&=0x20  // 0b1000 0000

#define START_LOOP asm("_loopStart:");
#define RESTART_LOOP asm("  JMP _loopStart");

#define START_PULSE_CHECK asm("_pulseCheckStart:");
#define SKIP_TO_PULSE_CHECK asm(" JMP _pulseCheckStart");

uint8_t btOutput;
int intent, extent;
uint8_t cache[8] = {0x00, 0x00, 0x00, 0x00, 0x00, 0x00, 0x00, 0x00};
bool checkedLastTime = false;
bool shouldBrake;
Servo servo;
uint8_t cycleCount = 0;
uint8_t ledState = 0xFF;

ISR(USART_RX_vect)
{
  uint8_t uart_rx = UDR0;
  uint8_t intent = uart_rx / 32;
  uint8_t extent = uart_rx & 0x1F;
  cache[intent] = extent;

  if (intent == 7) cache[intent] = uart_rx;
  
  if (intent > 4 || (shouldBrake && intent != 2 && intent != 3)){
    // Power was adjusted
  } else {
    if (intent == 1){
      if (extent) IN1_HIGH;
      else IN1_LOW;
    } else if (intent == 2){
      if (extent) IN2_HIGH;
      else IN2_LOW;
    } else if (intent == 3){
      if (extent) IN3_HIGH;
      else IN3_LOW;
    } else if (intent == 4){
      if (extent) IN4_HIGH;
      else IN4_LOW;
    }
  }
}

int getDistance() {
  TRIG_LOW;
  delayMicroseconds(2);
  TRIG_HIGH;
  delayMicroseconds(10);
  TRIG_LOW;
  delayMicroseconds(2);
  return (int)pulseIn(ECHO_PIN, HIGH, 1300) / 58;
}

void brake(){
  ENA_HIGH;
  ENB_HIGH;
  IN1_LOW;
  IN2_LOW;
  IN3_LOW;
  IN4_LOW;
}

void spinRight(){
  ENA_HIGH;
  ENB_HIGH;
  IN1_LOW;
  IN2_HIGH;
  IN3_LOW;
  IN4_HIGH;
}

void spinLeft(){
  ENA_HIGH;
  ENB_HIGH;
  IN1_HIGH;
  IN2_LOW;
  IN3_HIGH;
  IN4_LOW;
}

uint8_t steeringAngle(){
  uint8_t leftPower = (cache[0x06] & 0x1F);
  uint8_t rightPower = (cache[0x05] & 0x1F);

  return (rightPower > leftPower) 
  ? (87 + (rightPower - leftPower) * 3) 
  : (93 - (leftPower - rightPower) * 3);
}

void performTask(uint8_t task){
  if (task == 0x00) brake();
  else if (task == 0x01) spinRight();
  else if (task == 0x02) spinLeft();
  else if (task == 0x0F) cache[0x07] = 0x00;
}

void setup() {
//  Serial.begin(9600);
  UBRR0H = (unsigned char) (103>>8);
  UBRR0L = (unsigned char) 103;
  
  UCSR0B = (1<<RXEN0) | (1<<TXEN0);
  UCSR0C = (1<<USBS0) | (3<<UCSZ00);
  
  // Enable Serial completion interrupt
  cli();
  UCSR0B |= (1<<RXCIE0);
  sei();
  
  TRIG_ENABLE;
  ECHO_ENABLE;
  IN1_ENABLE;
  IN2_ENABLE;
  IN3_ENABLE;
  IN4_ENABLE;
  ENA_ENABLE;
  ENB_ENABLE;
  LED_ENABLE;
  
  servo.attach(SERVO_PIN);
}

int main(void){
  init();
  setup();

  START_LOOP;
  unsigned long start = micros();
  if (cycleCount == 0){
    if (ledState) LED_HIGH;
    else LED_LOW;
    ledState = ~ledState;
  }
  cycleCount = (cycleCount + 1) % 0x1F;

  if (!(cycleCount%4)){
    int dist = getDistance();  
    // Check if we should brake.
    shouldBrake = abs(dist) <= 20 && abs(dist) != 0;
  }
  
  checkedLastTime = !checkedLastTime;

  if (shouldBrake){
    // Ensure we shouldn't be braking or going in reverse
    if ( cache[0x07] != 0xE0 && (cache[0x02]&0x1F != 0x00 || cache[0x03]&0x1F != 0x00) ){
      // Just don't do anything I guess
    } else {
      brake();
      RESTART_LOOP;
    }
  }

  servo.write(steeringAngle());

  if(cache[0x07]){
    // IN1 has been updated
    performTask(cache[0x07] & 0x1F);
    RESTART_LOOP;
  }

  if (cycleCount < cache[0x05]) ENA_HIGH;
  else ENA_LOW;

  if (cycleCount < cache[0x06]) ENB_HIGH;
  else ENB_LOW;

//  Serial.println(micros() - start);

  RESTART_LOOP;
  return 0;
}

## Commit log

2019-09-22 Switched to gyroscope controls, updated UI, added center, neutral, and show data button
2019-09-23 Added icon, SteeringService, sends over bluetooth, many bug fixes and improvements
2019-09-23 Improved steering and reduced data sent to changes in state
2019-09-23 Added initial driver schematics
    [Driver.brd, Driver.sch]
2019-09-24 removed prints from main
2019-09-24 Changed ∆ to d
2019-09-24 switched to use echo rising and falling edge
2019-09-24 added print statement
2019-09-26 added arduino code, minor app changes
2019-09-26 Switched to single byte control method
2019-09-26 Allow for full gyro controls
2019-09-26 Added forward collision avoidance
    [EE437_Car.ino]
2019-09-29 fixed bug where max throttle came out as no throttle
2019-09-29 Added tasks to arduino code, updated signal refresh speed
2019-09-30 Added Arduino Shield schematic
    [ArudinoShield.brd, ArudinoShield.sch]
2019-09-30 renamed component, updated ignore
    [ArudinoShield.brd, ArudinoShield.sch]
2019-09-30 added routes to board
    [ArudinoShield.brd, ArudinoShield.sch]
2019-09-30 reduced schematic
    [ArudinoShield.brd, ArudinoShield.sch]
2019-09-30 Reduced shield schematic
    [ArudinoShield.brd, ArudinoShield.sch]
2019-10-01 added board image
2019-10-02 upgraded schematic picture
2019-10-02 higher res board picture
2019-10-02 added values, updated gitignore for eagle files
    [ArudinoShield.brd, ArudinoShield.sch]
2019-10-02 updated schematic for proper pinout from L298 and added supply voltage terminal block
    [ArudinoShield.brd, ArudinoShield.sch]
2019-10-02 updated board and schematic images
2019-10-02 updated schematic and board
    [ArudinoShield.brd, ArudinoShield.sch]
2019-10-02 updated power trace size
    [ArudinoShield.brd, ArudinoShield.sch]
2019-10-02 added ground plane, updated layout
    [ArudinoShield.brd, ArudinoShield.sch]
2019-10-02 updated board and previews
    [ArudinoShield.brd, ArudinoShield.sch]
2019-10-03 fixed L298 pin 8 not being reliably grounded
    [ArudinoShield.brd, ArudinoShield.sch]
2019-10-03 By hand rework of board layout, no vias
    [ArudinoShield.brd, ArudinoShield.sch]
2019-10-03 increased minimum trace width
    [ArudinoShield.brd]
2019-10-03 minor changes, updated images
    [ArudinoShield.brd, ArudinoShield.sch]
2019-10-03 minor board changes
    [ArudinoShield.brd, ArudinoShield.sch]
2019-10-03 reworked to fit on top of arduino
    [ArudinoShield.brd]
2019-10-03 minor changes
    [ArudinoShield.brd]
2019-10-03 updated schematic and board to use DC jack
    [ArudinoShield.brd, ArudinoShield.sch]
2019-10-04 shifted L298 to make room for heat sink
    [ArudinoShield.brd]
2019-10-09 added new arduino code for custom board
2019-10-09 moved all EAGLE files into own folder
    [ArudinoShield.brd, ArudinoShield.sch, Driver.brd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]
2019-10-14 updated to power peripherals from regulator, updated line width
    [ArudinoShield.brd, ArudinoShield.sch]
2019-10-14 updated images
    [ArudinoShield.brd]
2019-10-14 moved Vin inside board
    [ArudinoShield.brd]
2019-10-14 added breadboard layout
    [ArudinoShield.brd]
2019-10-15 Began New Arduino Board
    [ATMegaBoard.brd, ATMegaBoard.sch]
2019-10-16 added standalone board
    [ATMegaBoard.brd, ATMegaBoard.sch]
2019-10-17 updated ATMegaBoard, added CAM files
    [ATMegaBoard.brd, ATMegaBoard.sch]
2019-10-17 Switched to female header for HC05
    [ATMegaBoard.brd, ATMegaBoard.sch]
2019-10-17 compressed board
    [ATMegaBoard.brd, ATMegaBoard.sch]
2019-10-18 Fixed bug where unable to reconnect when disconnected from board
2019-10-18 added servo support, reduced to single cache with intent as indexing
2019-10-18 switch cache to bytes not ints, added reverse on sensor braking
    [EE437_Car.ino]
2019-10-18 First version of reduced board
    [ATMegaBoardReduced.brd, ATMegaBoardReduced.sch]
2019-10-18 updated layout
    [ATMegaBoardReduced.brd]
2019-10-18 minor layout changes
    [ATMegaBoardReduced.brd]
2019-10-21 set reset pin high added ground pins
    [ATMegaBoardReduced.brd, ATMegaBoardReduced.sch]
2019-10-21 shifted HC-SR04 away from ATMega
    [ATMegaBoardReduced.brd]
2019-10-22 minor board updates
    [ATMegaBoard.brd, ATMegaBoard.sch, ATMegaBoardReduced.brd]
2019-10-22 updated board to change mounted orientation
    [ATMegaBoard.brd, ATMegaBoard.sch]
2019-10-22 updated for final board decision, added parts list
2019-10-22 -Isaiah added LED boards
    [LEDs.brd, LEDs.sch]
2019-10-22 updated output for LEDs
    [ATMegaBoard.brd, ATMegaBoard.sch]
2019-10-22 expanded LED lighting to be 1 to 1
    [ATMegaBoard.brd, ATMegaBoard.sch]
2019-10-23 increased clearance between LEDs and D6
    [ATMegaBoard.brd]
2019-10-28 set EN on HC-05 to +5v
    [ATMegaBoard.brd, ATMegaBoard.sch]
2019-10-29 removed DPM of PORTD from brake
2019-10-30 reworked distance measurement methodology
    [EE437_Car_Optimized.ino]
2019-10-30 updated for using custom PWM
2019-11-01 implemented UART interrupt, enabled GPIO using asm macro, reduced main loop if statements
2019-12-04 fixed no braking bug
    [EE437_Car_Optimized.ino]

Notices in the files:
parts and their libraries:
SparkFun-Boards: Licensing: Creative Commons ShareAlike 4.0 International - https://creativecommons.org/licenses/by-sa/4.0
